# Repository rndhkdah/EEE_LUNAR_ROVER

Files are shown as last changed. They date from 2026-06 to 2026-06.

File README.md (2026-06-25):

# EEERover Specifications and Technical Guide
---

This GitHub project contains information on our electronics design project.

You will find
 - [Project Brief](doc/brief.md)
 - [Technical Hints](doc/README.md)
 - [A Marking Scheme](doc/deliverables-and-mark-scheme.md)
 - [Starter code for the Adafruit Metro M0 Express module](metro-starter-arduino/README.md)
   - [Starter code as a PlatformIO project](metro-starter-pio/README.md)
 - [Chassis design files](mech/)

---

## Project Management & Tasks

Quick links to our project planning and tracking documents.
You can fill in the task by yourself, cause I'm just copying the format you use on Notion. I do not know exactly what are the use of these.

- [Web UI Remote Control (Live Demo)](https://Albert14736.github.io/EEELunarRover2526-main/Sync%20files%20on%20GitHub/Tasks/SoftWare%20stuff/remote_ui_test.html) - Direct link to our deployed rover control interface (Phone/Desktop compatible).
- [Group 10 Master Doc (from Google Docs)](Sync%20files%20on%20GitHub/EEE%20Lunar%20Rover%20Group%2010.md) - **If you find it annoying to update multiple tracker files, just dump your progress, notes, or code snippets here** I will review this document regularly and organize/distribute the information into the proper folders for us.
- [Project Logbook / Diary](Sync%20files%20on%20GitHub/diary.md) - Our team's daily diary to record meetings and what we have achieved.
- [Team Workspace Guide](Sync%20files%20on%20GitHub/README.md) - [To be filled]
- [Demo](Sync%20files%20on%20GitHub/Projects/Demo.md) - [To be filled]
- [Interim Presentation](Sync%20files%20on%20GitHub/Projects/Interim%20Presentation.md) - [To be filled]
- [Report](Sync%20files%20on%20GitHub/Projects/Report.md) - [To be filled]
- [Parts Tracker](Sync%20files%20on%20GitHub/Tasks/Parts%20Tracker.md) - [To be filled]

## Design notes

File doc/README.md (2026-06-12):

# EEELunarRover Technical Guide

This guide has three main aims:
 - Document the additional hardware that you are provided with to get started
 - Specify the processes you will need to develop your design (e.g.~ordering components)
 - Provide some implementation ideas that you may find useful
	
 Most of the contents of this guide is advisory. You do not have to use your EEEBug or the items in the starter kit if you wish to pursue different ideas.
	
 ## Expansion Kit
 You are provided with some parts to use with your Lab-in-a-Box kit to get started:
 
| Qty | Description |
| --- | --- |
| 1 | Rock simulator  |
| 1 | Breadboard  |
| 2 | USB-A to Micro USB cable  |
| 2 | H-Bridge Motor Driver Module |	
| 2 | Adafruit Metro M0 Microcontroller Module |
| 2 | Adafruit WINC1500 WiFi Shield |
| 2† | Magnet |
			
You are given one expansion kit per group in your allocated shelf.
It is designed for use with your existing EEEBug chassis.
At the rear of the chassis is a mounting point for the Metro board and the central PCB has mounting points for the motor driver module.
The breadboard, as you have already seen, is ideal for prototyping circuits.
Finally, the design of the chassis is available to download that you can produce your own version.
    
### Motor Driver

The project kit contains a motor driver module to make it easy to control power to the motors.
The motor driver is an integrated *H Bridge* with decode logic, illustrated below.
The H-bridge allows current to be driven in either direction through the central load by connecting one terminal to the positive supply and the other to ground.

Circuit diagram of an H-bridge with logic decoder

The module contains two H-bridges, one for each motor.
Each channel has two digital inputs, DIR and PWM, which are decoded and used to control four MOSFETs.
The MOSFETs are driven with binary inputs so that they act as switches and the impedance is either very low or very high.
The motor driver module plugs into the motor power connectors on the EEEBug PCB.

The module inputs can be connected directly to digital outputs on the Metro board.
DIR controls the motor direction and the motor speed can be controlled by applying a rectangular waveform to the PWM input and varying the duty cycle — use `analogWrite()` in the Arduino API to generate a PWM signal.
			
### Metro M0 board

The Adafruit Metro M0 Express board is a embedded computing platform based on an ARM M0 microcontroller and compatible with the Arduino form factor, libraries and development tools.
It is programmed in C++ and features digital inputs and outputs, inputs with digital-to-analogue conversion and PWM outputs. Internet connectivity is provided by a Adafruit WINC1500 WiFi Shield, which plugs into the Metro board.

You are provided with demonstration code that shows the use of basic functions of the Metro board.
The WiFi interface is used to host a basic webpage, which you will see hard-coded into the demonstration code.
The webpage provides two links which, when pressed, turn on and off the onboard LED.
Use the Arduino Serial Monitor to connect to the board via USB and you will see some debug messages reporting on the connection status.
Whenever the webpage is retrieved you will see the HTML request made by the web browser.
			
Arduino is a popular platform for prototyping and you will find a lot of information and many code examples on the internet.
Use these resources but beware that many are provided by third parties and may not be well-written or even correct!
			
### Starter code

This repository contains [microcontroller code](../metro-starter-arduino/README.md) to get you started.
You can continue to use Arduino IDE as in the lab skills work, or you can develop with Visual Studio Code and Platformio.
			
 ### Connections and Power
 
> **Warning**
> 
> The logic level of the Metro board is 3.3V, which is supplied by an on-board voltage regulator.
> You will damage the board if you connect the input/output pins to a voltage greater than 3.3V.

Use potential dividers to reduce voltages greater than 3.3V and measure the output voltage of your circuits before connecting them to the inputs of the Metro board.
The safest option is to design add-on circuits with a 3.3V power supply.
Digital inputs should be 0V for logic low and 3.3V for logic high.
Analogue inputs should be in the range 0--3.3V.

Metro M0 Express Pinout
*Pinout for the Metro M0 Express module from [Adafruit](https://learn.adafruit.com/adafruit-metro-m0-express/pinouts)*

The pin locations and functions are broadly compatible with the Arduino layout used on the Orangepip Kona328 board used in the Microcontroller lab experiment.
The I/O pins pass through the WiFi Shield when it is connected, but the pins labelled CS, IRQ and RST on the WiFi Shield (Arduino pins 5,7 and 10) are used by WiFi and can't be used for other purposes. 

The Metro board can be powered by USB, the power jack or the EEEBug batteries.
To connect to the EEEBug batteries you will need to make the following connections between the Metro board and the EEEBug PCB:

- 5V → 5V
- GND → GND

> **Warning**
> 
> Always check connections before switching on the power.
> You may damage the microcontroller if you make a mistake
			
You can use the 5V or 3.3V nodes to power your own circuit.
It is not recommended to use Vin or Vbatt, since the voltage of these will vary depending on the power source.
The motors will run slowly if the battery is not available.
			
Simplified circuit diagram of the Metro M0 Express and EEERover PCB power supplies

*A simplified diagram showing the connection of the Metro M0 Express and EEERover PCB power supplies*
			
 ### Rock simulator
      
Your prototype will be developed and tested using rock simulators: electronic devices which can replicate the characteristics of the real rocks.
A rock simulator is included in your kit to aid development.
 
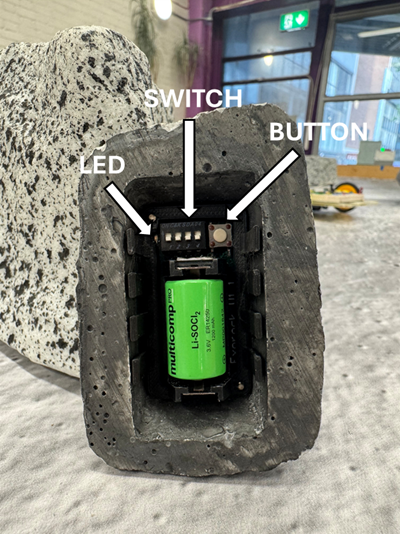
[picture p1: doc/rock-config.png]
User interface of the rock

					
The rock is configured by setting a group of DIP switches on its internal PCB. The switch, button, and LED are accessible without removing the PCB from the rock simulator.
A push button is used to turn it on and off, and an LED indicates when it is active.
A flow chart depicting the operation of the rock is shown below.
From standby (inactive) mode, press the button to turn on and observe the LED flashes to determine whether the battery has sufficient charge.
After the battery display sequence is complete the rock begins emitting signals according to the mode set up on the DIP switches.
The LED flashes a code at intervals to confirm the mode selection and indicate operation.

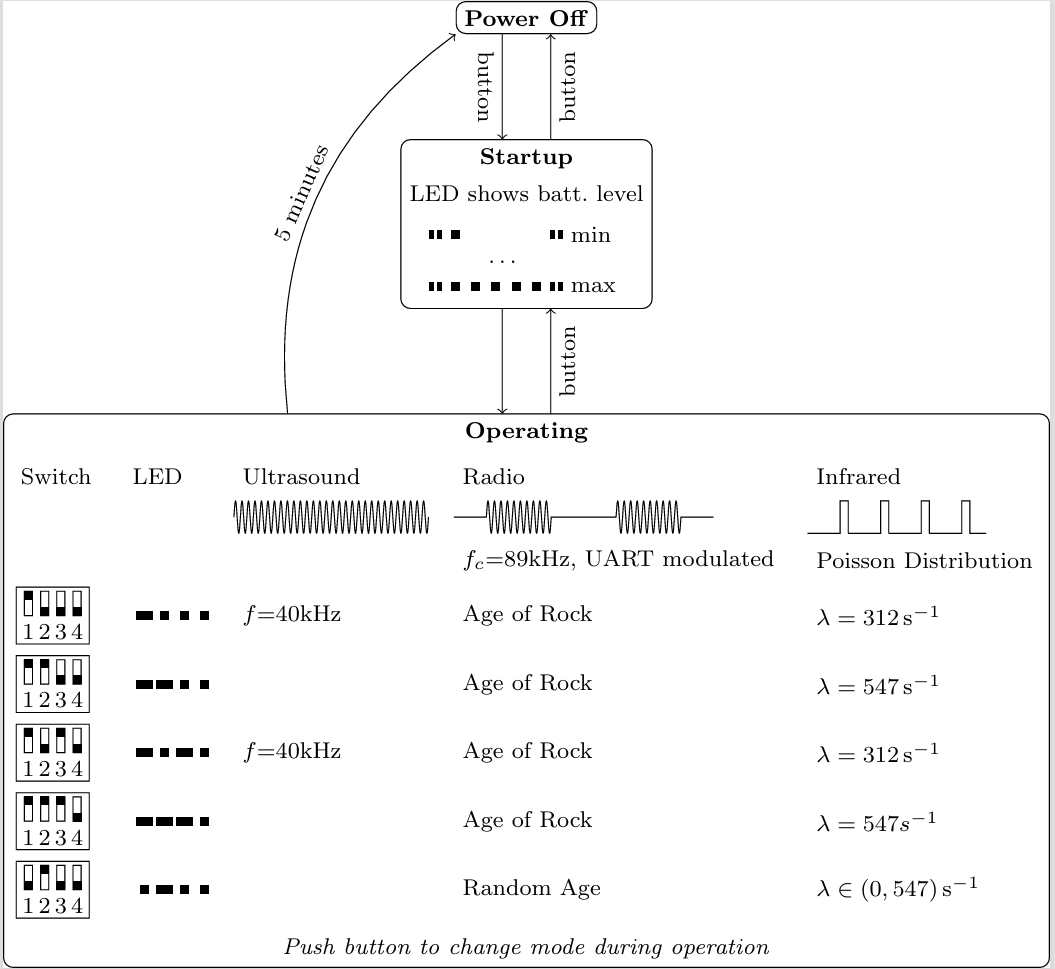
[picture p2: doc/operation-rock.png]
Operation flow chart for rock simulator


In normal operation, the rock communicate its age via radio — this will be the mode used in the final demonstration.
Other mode is available to help testing:
- The rock can communicate a random age and Poisson rate λ∈(0,547) s<sup>-1</sup>, which will change each time it is restarted.
		
Pushing the button during operation will reset the rock — this is necessary to change the operation mode.
A second press soon afterwards will turn the device off.
If the rock is left operating for five minutes it will automatically power off to preserve the battery.
			
The rock cannot simulate the magnetic property in an readily-configurable manner so you are provided with a small magnet to test this functionality.
In the demo, magnets will be placed inside a rock.
With the orange disc flat on a surface, the magnetic field is orientated down with the orange disc:

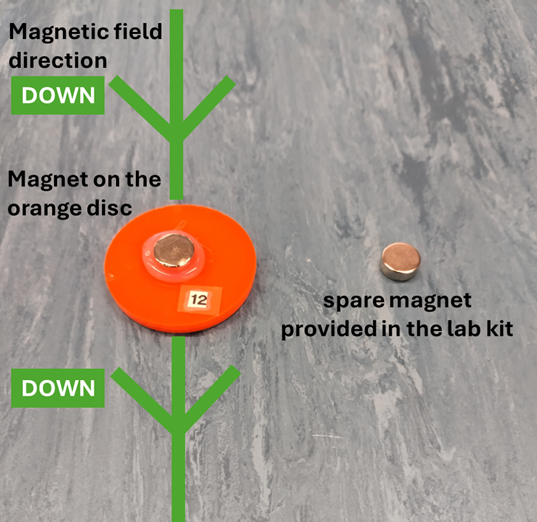
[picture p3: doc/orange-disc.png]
Magnetic field direction on an orange disk. With the disc flat on a surface, the magnetic field is orientated down with an orange disc


The radio signal is emmitted from a coil antenna in the plane of the PCB.	
			
 ## Components and Construction
 ### Ordering components

Each project group has a budget of £60 to cover all the additional components you'll need for designing and building your prototype. Each group must assign one member as the approver for their component orders. Orders will only proceed after approval from the approver of your group to prevent misordering or duplicate orders.

Your approver will order components by using Online Order Form in [EEE Stores Website](https://www.imperial.ac.uk/electrical-engineering/internal/stores/).

You will receive an email when the parts are available for collection from Stores on level 1, near the lifts. Orders, assuming the items are in stock, will take up to a week to arrive. You can order some components directly from stores stock and these will usually be available for collection sooner.
			
Please be aware of the following rules and common pitfalls when ordering components:
 - You must only order items that you can use safely. If you have any doubts about this then talk to a member of staff before ordering. Do not order batteries, chemicals (including glue), tools or mains-powered equipment/parts without consulting staff.
 - Always check that the supplier holds sufficient stock. If an item is out of stock it will be placed on back-order and it may take months to arrive. Try to find an alternative part or supplier instead.
 - Some suppliers offer stock from sister companies around the world. Do not order any items which warn about additional delivery charges.
 - Many electronic components are *surface mount*. This means that they sit on flat pads on a PCB instead of having flexible leads to insert into a prototyping board. They are also usually very small. You will find surface mount components difficult to use so avoid them by checking item descriptions and datasheets carefully.
 - You need to maintain the goodwill of the stores staff to order parts for this project and future projects. Do not chase the staff for your order until one week has passed from placing the order. It is your responsibility to order in good time and to check parts for suitability and availability.
			
### Making a new chassis
This repository contains design files for the EEEBug chassis.
You can design your own version using this as a template.
You will see that cut lines are drawn in red and engrave lines are drawn in blue.
Laser cutting removes a tapering width of material known as a *kerf*, which for 3mm acrylic is typically 0.1mm at the bottom of the material and 0.3--0.4mm at the top. Hence, cut edges are not vertical and external dimensions will be slightly smaller than drawn and internal dimensions slightly larger than drawn.

Designs for laser cutting must be submitted in PDF format.
Multiple parts can be placed on the drawing as long as they fit into an area of 600mm x 300mm.
Add engraving to identify your group as the owner.
You are strongly recommended to check your design by printing it on paper first — the scaling will be identical as long as the PDF file is printed at 100% scaling.

### 3D printing and Workshop facilities
A basic workshop is available in the lab.
Talk to Vic if you want to use it and be prepared to explain exactly what you want to do and demonstrate that you are capable of doing it safely.
You can also have components 3D printed if you are willing to learn the necessary design techniques independently.
Talk to Amine in the technicians' office if you would like to use 3D printing.
			
## Implementation Hints
The characteristics of rocks from the design brief are:
- Age (Radio)
- Types (Infrared, ultrasonic)
- Magnetism
			
### Age
  
The rock's age is encoded as ASCII characters and framed as UART packets in radio signal.

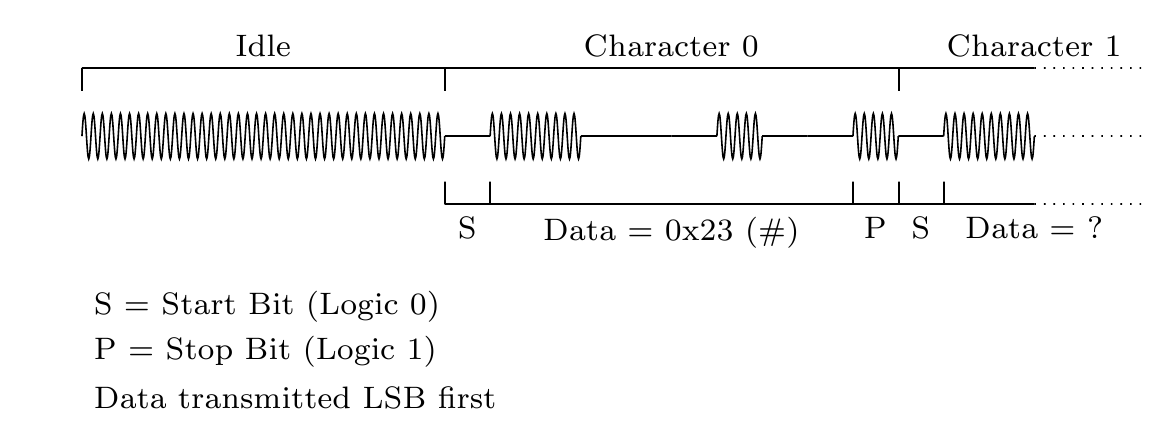
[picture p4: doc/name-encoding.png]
Name encoding


Radio communication uses a carrier frequency of 89kHz, modulated with a form of amplitude-shift-keying, where an amplitude of 0 represents logic 0 and an amplitude greater than 0 represents logic 1. 
First you will need to pick up the radio waves via an antenna. Then, you will need to convert the radio waves (ASK modulated radio signal, UART - given in the operation flow chart for rock simulator) into a signal.
You can use a tuned coil antenna, which is essentially an air-cored inductor with a reasonably large diameter that you can make by coiling wire.

This inductor can then be used in a tuned circuit that will be most sensitive at the resonant frequency.
The lab has *LCR Bridge* instruments that can tell you the inductance of your inductor.

The signal amplitude generated by your antenna will be small, so it will need amplification before you can extract the data.
The microcontroller will struggle to sample the radio signal at its carrier frequency so you will need to perform demodulation with *envelope detection* to produce a signal which indicates the amplitude of the signal.
The easiest way to do this is by rectification, but you may need a *precision rectifier* if your signal does not have enough amplitude to accommodate the voltage drop caused by a simple diode.
A precision amplifier needs an opamp with a relatively high slew rate. 

After demodulating the signal, you can convert the demodulated signal into a binary signal with a comparator, which compares the amplitude against a threshold.
A threshold can be set with a potential divider, or a more advanced approach is to derive it automatically from the average level of the signal with a low-pass filter.

As you saw in the Lab Skills work, microcontrollers have UART communication built in, and you can use your Metro module to automatically decode the demodulated binary signal into bytes.
In the Orangepip, communication to the host PC used the same UART port as the signals presented on pins 0 and 1.
However, the Metro board has two independent UART ports so you can use one to send debugging information over USB and a different port on pin 0 to receive messages from the rock.
The two ports can operate at different bit rates.
			
### Types
The types of a rock is indicated by an infrared signal pulse rate with a Poisson distribution, ultrasonic signal and magnetic fields.
For infrared signal, you have already made a light sensor as part of the EEEBug and most silicon-based photosensors (such as the EEEBug phototransistor) are just as sensitive to infrared as visible light.
You will need to measure the infrared pulses rate and this can be done with analogue or digital methods.

The optical power given by the rock is weaker than the light source you used for the EEEBug so you may need to amplify the output.
Ambient light will cause interference and this can be filtered out by using a sensor that is only sensitive to the wavelength of the rock emission (950nm) and by using electronic filters.
Many sources of electric light have a strong frequency component at 100Hz due to the rectification effect of the 50Hz AC source.

The infrared pulse rate is approximately λ=547 s<sup>-1</sup> or λ=312 s<sup>-1</sup> depending on the type of a rock. The pulse width of the infrared signal is just 50μs and the amplitude that you observe will be reduced if you filter out the high frequency harmonics. Low-pass filtering may smooth out the edges of the pulse and make pulse rate measurement less accurate. There can even be a problem with the sensor itself, since all optical sensors have a capacitance that acts to introduce a low-pass filter. There may be a trade-off between the speed and the sensitivity of your sensor.

A recommended method for measuring random infrared pulse rates on a lab oscilloscope is described below.

1. View pulses on the oscilloscope with a 10ms timebase.
2. Add measurement for 'Count' (positive or negative pulse depending on signal).
3. Use the 'single' button to capture and count one screen of the signal. The oscilloscope shows 12 divisions at 10ms, so the measurement is the pulses counted in 120ms.
4. You can confirm that the count measurement matches the number of pulses visible on the screen, but you should use the 'Zoom' view to be able to distinguish closely spaced pulses.
5. Use the single button to make as many measurements as necessary to get a statistically significant result.

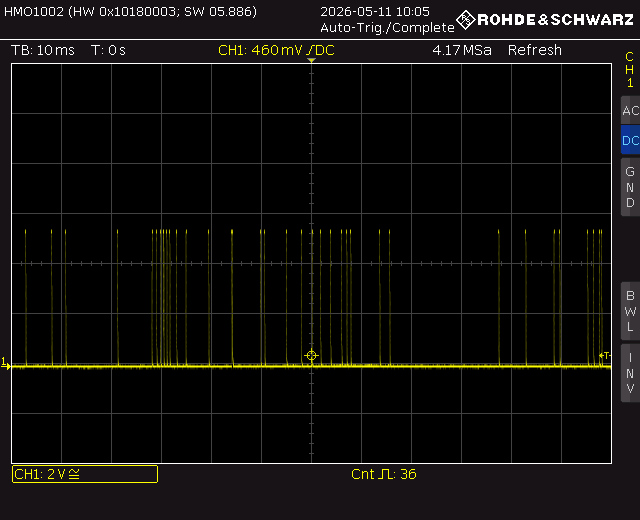
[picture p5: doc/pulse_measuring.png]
Measuring the infrared pulses rate on the oscilloscope


For the ultrasonic system, you will need to pick up the ultrasonic signal by placing a suitable ultrasonic transducer near a rock. Then, the classification of the rock can be done based on the ultrasonic signal presence (40kHz) or absence.
			
### Magnetism
The magnetic field of the rock is static, meaning that it will not induce a current in a coil of wire unless that coil is moving.
A moving coil is a possibility, but there are also sensors and switches that can detect a static magnetic field.
Test any new components and read their datasheets to determine if any amplification or signal processing is required.
Many sensors are designed to detect if a mechanism is open or closed (e.g. a laptop screen), and they may not work well in this application because the magnetic field may be weak due to the distance of the sensor from the magnet.
Furthermore, you need to determine the direction of the magnetic field, whether it is up or down. In the demonstration, magnets will be placed inside a rock as shown below.

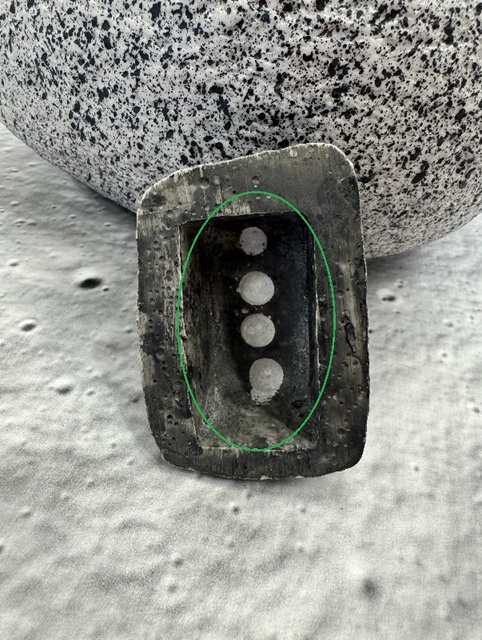
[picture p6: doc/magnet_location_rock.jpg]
Magnet location in rock

   
### Opamps
You may wish to implement amplification or filtering using an opamp.
There are many different opamps and they have different specifications.
Some manufacturers have parametric search facilities on their websites to narrow down the options based on your specifications. Use the opamp knowledge you obtained last term and conduct your research to choose suitable opamps for your applications.

There are some important parameters to consider:
- The opamp must operate at the available power supply voltage. Some opamps are design for use at higher voltage.
- You may need an opamp that offers *rail-to-rail* input and output, which allows you to make full use of the supply voltage.
- If the opamp output needs to switch quickly then the *slew rate* will be important. This will be a consideration in comparator and rectifier circuits. The LT1366 has a low slew rate.
- For high-gain circuits, check that the *gain-bandwidth product* is sufficient at the signal frequency you are using.

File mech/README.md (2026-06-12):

 # Chassis Design Files
 
 These files contain the design for the original EEEBug chassis. You can use them to design a modified chassis for your EEERover. There are three formats:
 
 - .dxf - This is a technical drawing format for CAD software
 - .svg - This is a drawing format that you can edit with vector graphics software like Inkscape. The width of lines must be set to 0.01mm for the laser cutter to interpret them as linear cuts.
 - .pdf - Your production file for the technicians should be in pdf format. Print it on paper at 100% scale to make sure the dimensions are correct. Red lines (#FF0000) are a complete cut and blue lines (#0000FF) are for engraving.

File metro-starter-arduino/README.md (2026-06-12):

# EEERover starter code

This project is an example of setting up WiFi communication with the Metro M0 Express module using HTTP.
The microcontroller connects to a WiFi network and acts as a simple web server, returning a basic web page when it receives an HTTP request.
It also acts on certain paths in the HTTP request to switch an LED on and off when the client clicks buttons on the webpage.

## Building the project

Additional libraries are needed to use Arduino IDE with the Metro M0 board and WiFi module. [Follow the instructions from Adafruit](https://learn.adafruit.com/adafruit-metro-m0-express/arduino-ide-setup) to add support for the Metro M0 Express board in Arduino IDE. Alternatively, you can build the project in [Visual Studio Code using PlatformIO](../metro-starter-pio/README.md).
			
The WiFi communication functions are provided by the WiFiWebServer library, which also must be installed with the Library Manager. The library installs its own set of example sketches and has an [API reference](https://github.com/khoih-prog/WiFiWebServer). The demonstration code in this repository is based on these examples.

## Network configuration

The code is configured to connect to the EEERover network in the lab. You can give a different WiFi network and password, such as a mobile hotspot, by changing the appropriate lines in the code. You won't be able to connect to the College WiFi network, which uses a login. When the code starts it reports its IP Address on the serial monitor. You can connect to the microcontroller from a computer on the same WiFi network by typing this address into a web browser. WiFi functions are provided by the [WiFi101](https://www.arduino.cc/reference/en/libraries/wifi101/) library.

You may need to connect to the microcontroller when it is not connected with a USB cable, so you won't see the message reporting the IP address. You can fix the IP address to a certain value by setting `groupNumber` to your group number. The IP address will be `192.168.0.n+1`. You can only do this on the EEERover network because it has been configured to allow a certain range of static IPs.

## HTTP server

The [WiFiWebServer](https://github.com/khoih-prog/WiFiWebServer) library is used to handle HTTP requests from WiFi clients.
HTTP is the protocol used to access websites and it is used here because it allows the creation of a simple user interface using a web browser.

The server is configured in the `setup()` function using calls to `server.on()` to define what happens when requests are received.
Each HTTP request has a URI, which is the path of the resource that is requested. The server responds to three different URIs:
 - `/` The root path, e.g. `http://192.168.0.10/`
 - `/on` A request to turn the LED on, e.g. `http://192.168.0.10/on`
 - `/off` A request to turn the LED off, e.g. `http://192.168.0.10/off`

A different function is called when each request is received. A request to the root path returns the html code for the user interface. `/on` and `/off` set the LED and the reponse is the state of the LED, either `ON` or `OFF`.

### The web interface

The webpage built into the starter code is a basic user interface based on JavaScript and HTTP requests. `<button>` tags are used to define two buttons, which are formatted with some basic styling defined in the `<style>` section. Each button triggers a JavaScript function that is defined in the `<script>` section. In these functions, a [XMLHttpRequest](https://developer.mozilla.org/en-US/docs/Web/API/XMLHttpRequest/Using_XMLHttpRequest) object is used to send a HTTP request with its `send()` and `open()` methods. 

An inline function is assigned to `xhttp.onreadystatechange`, which is called whenever a response is received to a HTTP request. The function updates the LED state text displayed on the page with the contents of the HTTP response. Remember that all the JavaScript functions are executed on the client web browser, not on the microcontroller module. You could host or store the webpage somewhere else entirely - you would just need to modify the URLs for the on and off HTTP requests to include the full hostname (IP address) of the microcontroller.

## Next steps

The code gives an example of sending information in both directions between the microcontroller and the remote client.
It can be extended to include all the data you need to control your rover and get data back.

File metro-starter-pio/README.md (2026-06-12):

# EEERover starter code for Platformio

Download Microsoft Visual Studio Code and install the Platformio extension. Open Platformio Home using the link in the Platformio sidebar or the 🏠 (home) icon on the bottom toolbar. Choose 'Open Project' and select the directory containg this README.

Build the project using the Build option in the Platformio sidebar or the ✓ icon on the bottom toolbar. Platformio will download the required libraries and board support package the first time you build the project.

Run the code by choosing 'Upload' or →. View the serial output using 'monitor' or 🔌. A terminal will open to show the serial output from the microcontroller.

Refer to the documentation for the [Arduino IDE version](/metro-starter-arduino/README.md) of the starter code for more information.

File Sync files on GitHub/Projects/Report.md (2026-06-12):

# Final Report & Reflection

**Date of Submission:** 11 June 2026
**Weighting:** 40%

## Deliverables
1. **Main Group Report**: Formal documentation of all technical and non-technical work. Justify all design decisions and include test results.
2. **Professional Reflection Forms**: Must be prepared individually and added to the appendix (Must pass component!).

## Proposed Report Structure
- **Introduction**: Project brief and objectives.
- **Hardware Design**: Circuit diagrams, op-amp calculations, sensor selection (e.g., SS49E hall sensor).
- **Software Design**: State machine, WiFi communication, UART decoding, filtering algorithms.
- **Testing & Results**: Oscilloscope screenshots, motor diagnostic logs (e.g., test on 13/05).
- **Project Management**: Budget tracking, task allocation, timeline.
- **Conclusion & Future Improvements**.

*Note: One team member should act as the overall editor to ensure consistency in style and content.*

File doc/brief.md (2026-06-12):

# ELEC40006 Electronics Design Project 
## Project Brief: EEELunarRover
	
## Introduction
	
The Electronics Design Project is one of the six modules that make up your first year of study.
It brings together theoretical and practical content from your lectures and labs with important industrial skills relating to product design, project management and team working.
		
You will work in tutorial groups of 6 people to complete the project.
It will be assessed with an interim interview, a final report that includes a professional reflection forms (must pass component), and a demo.
		
## Brief

You are requested to design a remotely-controlled lunar rover, EEELunarRover, that can survey the lunar surface and classify the rocks there.
Using a variety of electromagnetic signals, you must find out the age and types of each rock.

Artificial Lunar Surface
  
A prototype of the design must be built and tested in an artificial environment in the lab.
The quality of the design will be assessed against the following criteria:
- Is it possible to find the characteristics of all the rocks?
- Is the design cost and weight effective?
- Is the rover manoeuvrable enough to negotiate the environment?
- Is the construction robust and reliable?
- Is the remote control interface logical and easy to use?
	
## Characteristics of the rocks
### Age

The rocks transmits data via a radio using 89kHz carrier frequency, which is modulated with two-level *amplitude-shift keying* (on off modulation).
The age is encoded using ASCII character codes in UART packets with 1 start bit and 1 stop bit.
The data rate is 600 bits per second and each rock's age is four characters long, including an initial `#` symbol. If you receive `#123`, it will mean the rock's age is 1.23 billion. 
	
Rock age encoded in radio frequency
	
### Types

The rocks look same, but their colour and shape are superficial. You will need to examine other characteristics - infrared, ultrasonic and magnetic - to determine the types of a rock. The rocks emit radiation events randomly in time with a Poisson distribution which can be measured using an infrared detector on your rover. Infrared pulse rate will give information about the radioactivity levels of the rocks. Your rover will count the radiation event (infrared pulse rate) in the rocks to classify their radiactivity and type. Basaltoid and Lunarite are more radioactive than Gravion and Regolix. 

The characterisitics of each types are defined below:

| Types  | Infrared | Ultrasound | Magnetic |
| --- | --- | ----- | --- |
| Basaltoid  |λ=547 s<sup>-1</sup> | 40kHz | Down |
| Gravion  |  λ=312 s<sup>-1</sup> | | Down |
| Regolix | λ=312 s<sup>-1</sup>  | 40kHz | Up |
| Lunarite | λ=547 s<sup>-1</sup> |  | Up |

> [!NOTE]
> Please expect small deviations in the given values for Infrared pulse rate.

## Deliverables and assessments
	
The project will be assessed with an interim interview, a final report that includes a professional reflection forms (must pass component), and a demo with and interview and head-to-head competition.

### Interim Presentation

**Date of assessment:  28 May 2026**

The interim presentation is an opportunity to show your progress mid-way through the project.
You should prepare a presentation showing your high-level design, research and technical progress so far.
You should also present a plan for the remaining work to complete the project.

Marks weighting: 20%
	
### Report

**Date of submission:  11 June 2026**

The report is a formal documentation of all the technical and non-technical work you have done on the project.
The report should justify all your design decisions and include test results of various aspects of your prototype.
One team member should act as overall editor to ensure that the report is consistent in style and content.

Marks weighting: 40%

### Professional Reflection Form

**Date of assessment:  11 June 2026**

Professional Reflection Forms will be prepared individualy and added to your group project report appendix.

Marks weighting: 0% (must pass component)

### Demo

**Date of assessment:  16 June 2026**

The demo is your opportunity to present your completed project.
There are two parts to the demo:
1. An assessment of your rover on the lab bench, where your examiner will ask to see different functional aspects and assess your theoretical understanding of the implementation
2. A test of your rover on the demonstration arena, where multiple groups will compete to classify all the rocks in the quickest time.

Marks weighting: 40%
	
## Getting started
				
### EEEBug Expansion Kit
Your EEEBug has been designed to support modification for work on this project.
The Orangepip will be replaced with an ARM-based microcontroller platform with a WiFi module, but you can continue to develop code using the Arduino framework and IDE.
The central PCB has connections for a motor driver module, which will simplify the challenge of steering and reversing your rover.
			
### Sensing
You should use the outcome of your lab experiments to develop ideas for making sensors and analogue interfaces to detect the signals.
The EEEBug experiment showed you an example of an optical sensor.
The Passive Networks experiment (Autumn Term) introduces the concept of resonant circuits which, if the inductor is suitably constructed and orientated, will oscillate in the presence of radio waves of the correct frequency.
Magnetic sensors are not covered directly in the labs and you should carry out your own research in this area. Likewise ultrasonic transducers, which are usually designed to resonate at a specific frequency.
			
In certain cases you may wish to detect particular frequencies while blocking others, and you have explored to do this with passive and opamp-based circuits.
Some sensors will produce a weak signal that will need amplification.

Signals will need to be converted into the digital domain for transmission back to the rover operator.
Consider whether a binary input is sufficient, or you need to measure the voltage with more precision.
Research software libraries that can help you determine time-domain characteristics such as frequency or serial data encoding.
			
### Construction
Mechanical design is not a core component of the EEE/EIE degree so it is left to you to be innovative in the construction of your rover.
The EEEBug chassis is designed to be a useful platform but feel free to modify it, taking into account the budget and weight constraints.
			
You can download a computer-aided manufacturing (CAM) drawing of the chassis, which can be modified for reproduction in acrylic with a laser cutter.
Workshop facilities are available on arrangement with the lab technicians.
You may wish to consider 3D printing, though you will need to research and teach yourself the necessary techniques first.
3D printers are available to use with the help of the lab technicians.	

### Demo Environment
The demo environment has a grey coloured rubber flooring with some uncrossable obstacles.
Rocks will be distributed across the environment on the demo arena floor, spaced at least 500mm apart.
The arena is fitted with sensors in one area to check the weight of your rover. If your rover is heavier than 750grams, then it will fail classifying the rock in the weight sensitive zone on the lunar surface due to extremely loose and fragile surface there.

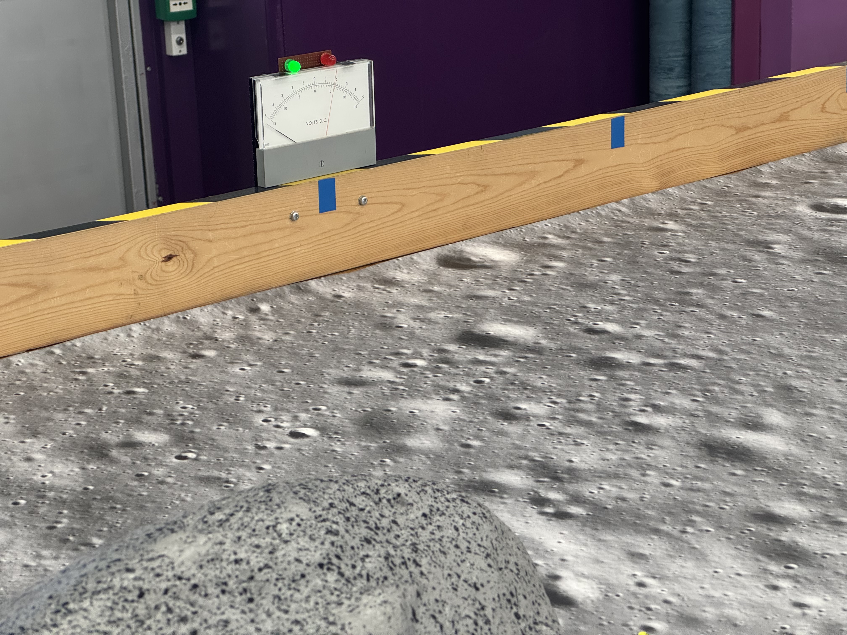
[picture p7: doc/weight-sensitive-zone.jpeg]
Weight Sensitive Zone


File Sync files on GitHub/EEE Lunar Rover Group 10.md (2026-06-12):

**<u>EEE LUNAR ROVER GROUP 10</u>**

<table>
<thead>
<tr>
<th>Group Members</th>
<th>Role</th>
</tr>
<tr>
<th>Mohammed Salem</th>
<th rowspan="2">Movement + User interface</th>
</tr>
<tr>
<th>Albert Ma</th>
</tr>
<tr>
<th>Devesh Kemani</th>
<th>Magnetism Detection</th>
</tr>
<tr>
<th>Christopher Koh</th>
<th>Project Manager + Infrared Detection</th>
</tr>
<tr>
<th>Wangmo Koo</th>
<th>Ultrasonic Detection + Parts IC</th>
</tr>
<tr>
<th>Ye Zifan</th>
<th>Age Detection</th>
</tr>
</thead>
<tbody>
</tbody>
</table>

**<u>TIMELINE</u>**

28 May - Interim Presentation

11 June - Report + Reflection Form

16 June - Demo

Components to order

| Item | Cost (pounds) | Min quantity |
|---|---|---|
| SS49E hall sensor | \<1 | |
| | | |
| | | |
| | | |
| | | |
| | | |

Steering

Receiving signals:

- Radio (age)

- Infrared

- Ultrasonic

- Magnetic

Weight (max 750g)

HARDWARE

[<u>https://www.keysight.com/used/gb/en/knowledge/guides/voltage-regulators</u>](https://www.keysight.com/used/gb/en/knowledge/guides/voltage-regulators)

**Report writing tips**

- See teams document

- Ensure narrative flow of report

- 

**INTERIM PRESENTATION**

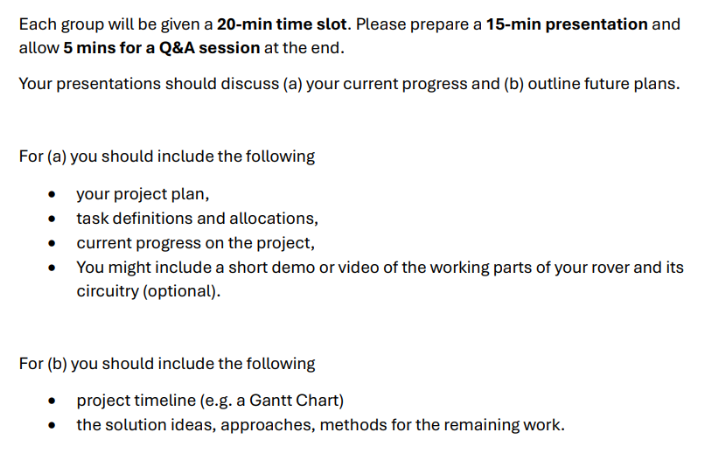
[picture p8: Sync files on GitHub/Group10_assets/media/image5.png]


**MAGNETISM DETECTION (DEVESH)**

<u>Sensing magnetic fields</u>

Hardware: SS49E hall sensor

Pin 1 (VCC): Connect to 3.3V on your Metro board.

Pin 2 (GND): Connect to GND.

Pin 3 (Output): Connect to an analog pin, like A0.

Metro M0 converts the voltage into a number 0-1023 using the analogue to digital converter

When no magneti near by - supply voltage = 1.65ishV and analogRead() will return a value near 512.

As a North pole approaches, the voltage rises toward 3.3V value moves toward 1023

As south pole approaches, the voltage drops toward 0V (value moves toward 0).

Magnetic field strength is proportional to r^3 so might only detect small changes. If the signal is too weak use Opamp as a non-onverting amplifier. MCP6002 opamp and build on breadboard

**Get op amp working, in slides talk about challenges that voltage signal isnt strong enough and solution w op amp. Do research into how magnetic sensor works and background knowledge for Q and A. run basic code from laptop. Write future part (talk about mount).**

**2-4 inclusive slides are my part**

Measure is +vs or-ve depending on which face of the sensor the magnet goes on, if magnet south puth faces magnet at all times.

0-1.8 in reality (in specs its0.2-1.8)

since 1V is when there is no sensor, the digital reading is 310.

Op amp

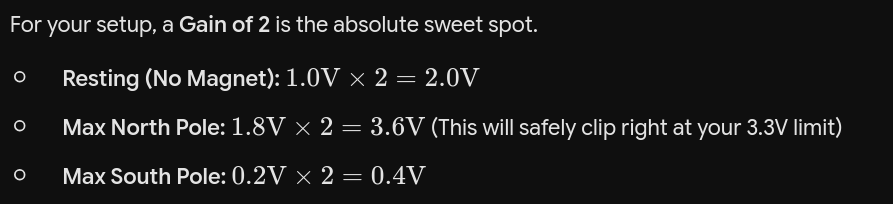
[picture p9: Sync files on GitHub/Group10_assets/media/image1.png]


Need to be literally touching the magnetic for 1.8v reding anyways so gain of 2 works as we will knoe if its in our face regardless that 0.3 v range we lose is negligible



Sample code:

void setup() {

Serial.begin(9600);

}

void loop() {

int sensorValue = analogRead(A0);

// 512 is the middle. We add a buffer of +/- 50 to avoid noise.

if (sensorValue \> 560) {

Serial.println("Magnetic Field: UP (North)");

} else if (sensorValue \< 460) {

Serial.println("Magnetic Field: DOWN (South)");

} else {

Serial.println("No strong magnetic field detected.");

}

delay(200);

}

- The motors or whatever else may create a magnetic field o their own so in the setup we need to account for that and records that value - 0 it out.

- Need to also account for rolling average, eg if value rises from 510 to 512 it doesnt necessarily mean we are moving closer to a rock. Therefore we should use a rolling average (eg the value of the reading is the average of the last 4 ‘snapshots’). Can achieve this simply with an array

- Need to account for other rocks magnetism in the code but i dont know how strong the other rocks magnetism will be

- 

Positioning:

- Point face (side with writing) down and point forward (closest to rock)

- Positing furthest away from motors

- 3D print a mount that can connect to the pins

const int hallPin = A0;

// Rolling Average Configuration

const int numReadings = 8; // Size of the filter window. Higher = smoother but slightly slower response.

int readings\[numReadings\]; // Array to store the raw ADC snapshots

int readIndex = 0; // Current position in the array

long total = 0; // Running sum of the array

int average = 0; // The smoothed output

// Baseline Configuration

int baselineValue = 0; // This will store the "zeroed out" resting value

void setup() {

Serial.begin(9600);

// --- 1. ZEROING OUT THE MOTORS (CALIBRATION) ---

Serial.println("Calibrating baseline...");

Serial.println("Ensure motors are running at default idle and magnets are far away.");

delay(2000); // Give the motors 2 seconds to spin up and stabilize their magnetic field

long calibrationTotal = 0;

int calibrationSamples = 50; // Take a deep average to find the absolute center

for (int i = 0; i \< calibrationSamples; i++) {

calibrationTotal += analogRead(hallPin);

delay(10);

}

// Set the new dynamic "middle" (Should be roughly around 310)

baselineValue = calibrationTotal / calibrationSamples;

Serial.print("Calibration complete. Baseline set to: ");

Serial.println(baselineValue);

// --- 2. PRE-FILL THE ROLLING AVERAGE ARRAY ---

// We fill the array with the baseline so the math doesn't start at 0 and falsely trigger

for (int i = 0; i \< numReadings; i++) {

readings\[i\] = baselineValue;

total += baselineValue;

}

}

void loop() {

// --- 3. ROLLING AVERAGE FILTER ---

// Subtract the oldest reading from the total

total = total - readings\[readIndex\];

// Read the newest raw value from the sensor

readings\[readIndex\] = analogRead(hallPin);

// Add the newest reading to the total

total = total + readings\[readIndex\];

// Advance to the next position in the array

readIndex = readIndex + 1;

// Wrap around to the beginning if we hit the end of the array

if (readIndex \>= numReadings) {

readIndex = 0;

}

// Calculate the smoothed average

average = total / numReadings;

// --- 4. MAGNETIC FIELD DETECTION ---

// Calculate how far we've deviated from the zeroed-out motor baseline

int deviation = average - baselineValue;

// Using a threshold of +/- 30 to avoid any remaining noise slipping through

if (deviation \> 30) {

Serial.print("North Pole Approaching! Signal Strength: ");

Serial.println(deviation);

} else if (deviation \< -30) {

Serial.print("South Pole Approaching! Signal Strength: ");

Serial.println(abs(deviation));

} else {

// If the deviation is between -30 and 30, we consider it clear

Serial.println("Clear. No strong magnetic rocks nearby.");

}

// A small delay for overall stability

delay(50);

}

**MOVEMENT (ALB**

**ERT)**

<u>How the robot can be controlled</u>

We should manually control the robot so that it can move towards the rock and gather sensor readings.

We can’t use the pins 5, 7, 10 since they are used by the WifiShield.

\[Reference to README file :

<span class="mark">The I/O pins pass through the WiFi Shield when it is connected, but the pins labelled CS, IRQ and RST on the WiFi Shield (Arduino pins 5,7 and 10) are used by WiFi and can't be used for other purposes.</span> \]

Therefore we should use other pins to control the motor.

THerefore we should use:

- Right : EN(8), DIR(9)

- Left : EN(11), DIR(12)

ENABLE wires are coloured orange

DIRECTION wires are coloured blue.

<u>13/05</u>

Connected PCB to Metro board and uploaded the code motor_move_v1 to test if the motors are connected properly.

\`\`\`v1

const int DIR_LEFT = 12, EN_LEFT = 11, DIR_RIGHT = 9, EN_RIGHT = 8;

void setup() {

Serial.begin(9600);

pinMode(DIR_LEFT, OUTPUT); pinMode(EN_LEFT, OUTPUT);

pinMode(DIR_RIGHT, OUTPUT); pinMode(EN_RIGHT, OUTPUT);

digitalWrite(DIR_LEFT, LOW); digitalWrite(EN_LEFT, LOW);

digitalWrite(DIR_RIGHT, LOW); digitalWrite(EN_RIGHT, LOW);

}

void loop() {}

\`\`\`

Test failed motors did not move, DC voltage 6.21 around battery terminal and 0.125A measured current through battery.

I found a wire that had not been placed properly (5V wire connecting board and PCB) fixed the issue and ran the code again.

Rewrote the code as well.

RESULT : LEFT motor was working fine but the right motor was not operating

The issue is that the motor on the right side works, however the pin12 is contested with the signal from the wifi module therefore we will use other pins to deliver the data. Suggested pins : DIR_LEFT = 2, EN_LEFT = 3

Rewritten code:\
const int DIR_LEFT = 12;

const int EN_LEFT = 11;

const int DIR_RIGHT = 9;

const int EN_RIGHT = 8;

// Speed for tests (0-255). 200 is a good starting point - high enough

// to overcome stiction, low enough to be safe on the bench.

const int TEST_SPEED = 200;

void setMotor(int dirPin, int enPin, int speed) {

// speed: -255 to +255. Positive = forward, negative = reverse, 0 = stop.

if (speed \>= 0) {

digitalWrite(dirPin, HIGH);

analogWrite(enPin, speed);

} else {

digitalWrite(dirPin, LOW);

analogWrite(enPin, -speed);

}

}

void stopBoth() {

setMotor(DIR_LEFT, EN_LEFT, 0);

setMotor(DIR_RIGHT, EN_RIGHT, 0);

}

void setup() {

Serial.begin(9600);

while (!Serial && millis() \< 3000) { ; } // wait briefly for serial monitor

pinMode(DIR_LEFT, OUTPUT);

pinMode(EN_LEFT, OUTPUT);

pinMode(DIR_RIGHT, OUTPUT);

pinMode(EN_RIGHT, OUTPUT);

stopBoth();

Serial.println("Motor diagnostic - no WiFi");

Serial.println("Watch each motor in turn.");

delay(1000);

}

void loop() {

// --- Right motor alone ---

Serial.println("RIGHT motor: forward");

setMotor(DIR_RIGHT, EN_RIGHT, TEST_SPEED);

delay(2000);

Serial.println("RIGHT motor: stop");

setMotor(DIR_RIGHT, EN_RIGHT, 0);

delay(1000);

Serial.println("RIGHT motor: reverse");

setMotor(DIR_RIGHT, EN_RIGHT, -TEST_SPEED);

delay(2000);

Serial.println("RIGHT motor: stop");

setMotor(DIR_RIGHT, EN_RIGHT, 0);

delay(1500);

// --- Left motor alone ---

Serial.println("LEFT motor: forward");

setMotor(DIR_LEFT, EN_LEFT, TEST_SPEED);

delay(2000);

Serial.println("LEFT motor: stop");

setMotor(DIR_LEFT, EN_LEFT, 0);

delay(1000);

Serial.println("LEFT motor: reverse");

setMotor(DIR_LEFT, EN_LEFT, -TEST_SPEED);

delay(2000);

Serial.println("LEFT motor: stop");

setMotor(DIR_LEFT, EN_LEFT, 0);

delay(1500);

// --- Both motors together ---

Serial.println("BOTH motors: forward");

setMotor(DIR_LEFT, EN_LEFT, TEST_SPEED);

setMotor(DIR_RIGHT, EN_RIGHT, TEST_SPEED);

delay(2000);

Serial.println("BOTH motors: stop");

stopBoth();

delay(2000);

}

The robot has its ends connected in the other way around.

We can fix this by the software or just connecting the wires to different parts around.

**AGE DETECTION (MOHAMMED + ZIFAN)**

**ULTRASONIC DETECTION (HARRY)**

**<u>Background</u>**

The rover will need to differentiate rocks based on the presence of multiple signals. The ultrasonic circuit will determine whether a 40kHz ultrasonic signal is emitted, after the presence of an infrared signal is found, it will be able to classify the type of rock.

Below is the table of types of rock and its corresponding signal presence

| **Types** | **Ultrasound signal presence** | **IR Rate** |
|---|---|---|
| Basaltoid | True | 547s^-1 |
| Gravion | False | 312s^-1 |
| Regolix | True | 547s^-1 |
| Lunarite  | False | 312s^-1 |

Ultrasonic presence separates {Basaltoid and Regolix } from the rock types, then the infrared rate will be used to distinguish within each pair (NO ultrasonic or when it exists). The role of this circuit would be to generate a clean logic signal representing the presence of an ultrasonic signal.

**<u>Design Process</u>**

**<u>Requirements</u>**

The circuit should follow these points;

- Detects the presence or absence of a 40kHz acoustic signal.

- Reject signal out of domain, which could be from motor vibration, ambient acoustic noise etc.

- Present the result to a microcontroller’s digital pin as a clean digital level.

- Able to detect presence of signal from a reasonable distance.

The raw signal from the 400SR-series receiver is a weak AC waveform and has a peak-to-peak value of roughly 10mV \[I need to measure the actual value in the lab\].

\[Picture of signal view on Oscilloscope, I can also use the auto-measure function\]

Therefore the signal should be amplified substantially before we can perform signal alteration operations.

**<u>Proposed Plan</u>**

Therefore we will be building a circuit with following stages to convert an AC signal received by the transducer and generate a clean DC logic signal.

Input : messy AC signal.

Output : Clean DC voltage output representing the presence of ultrasonic signal.

Transducer -\> Active Filter (Opamp with Band-pass-filters) -\> Envelope Detector -\> Comparator.

**<u>Expected change of signal</u>**

Expected change of signal would be as follows :

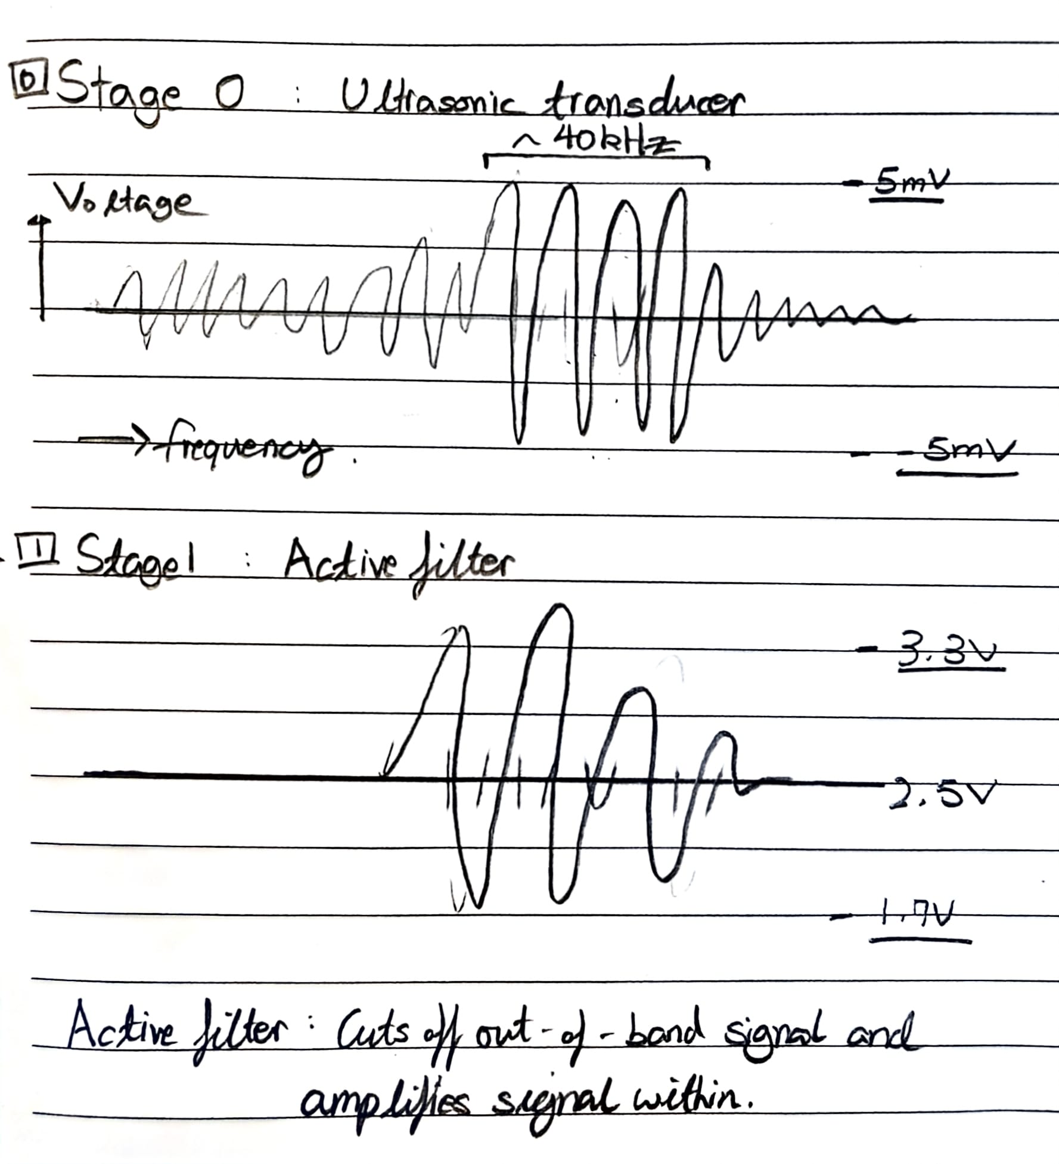
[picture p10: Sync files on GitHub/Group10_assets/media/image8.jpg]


> Unmodified signal from the transducer would be an AC signal with weak amplitude.

—-------------------------------------------------------------------------------------------



This part of circuit is an \`Active Filter\` This is used to filter out the parts that are out of band and amplify the signal within the specified range of frequency. We should also set up a

bias point around 2.5V to avoid

clipping the -ve part of the signal.

—---------------------------------------------------------------------------------------------

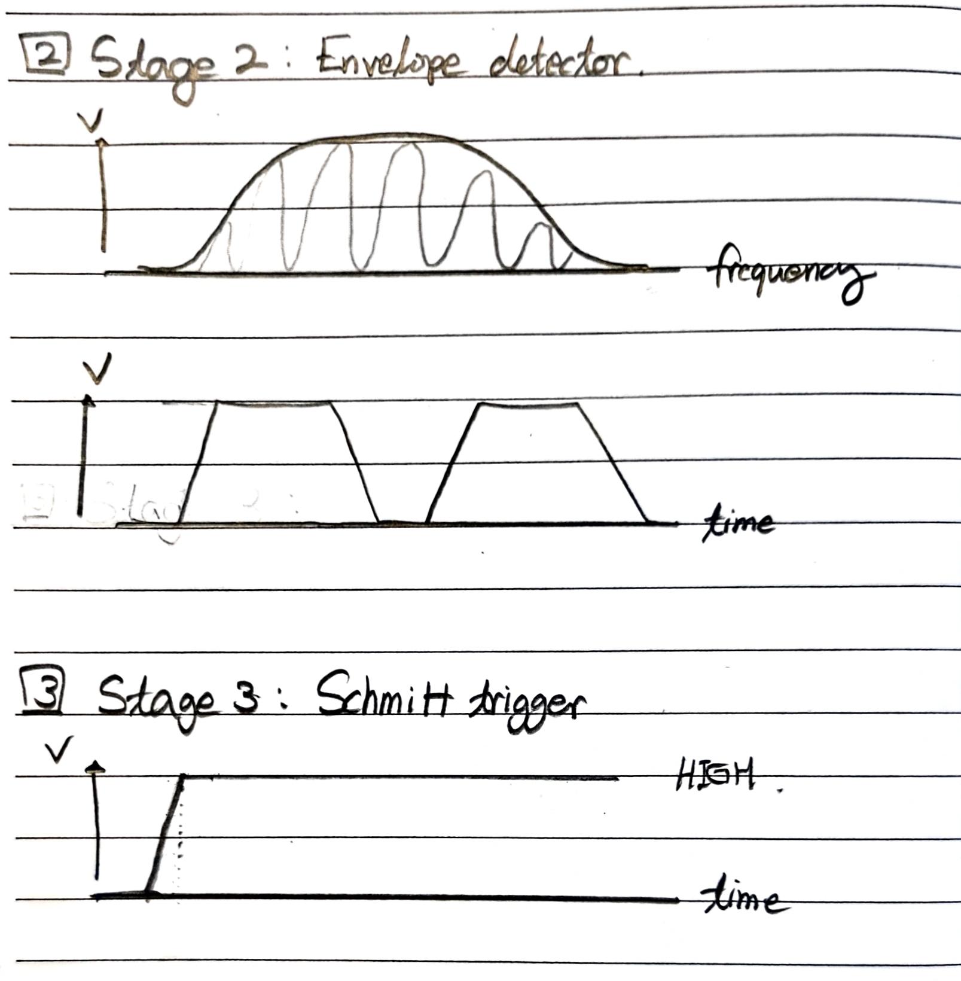
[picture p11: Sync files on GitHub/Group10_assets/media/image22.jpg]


Envelope Detector is used to smoothen out the alternating signal.

—---------------------------------------------------------------------------------------------

> Schmitt Trigger converts those pulses into a clean digital signal. With a high voltage outlining the presence and 0V representing the absence.

**<u>Component Selection</u>**

1.  Ultrasonic Transducer. (Used for stage 0)

Write about MCP6022, mention that its frequency is centered around 40kHz. Why would that be good?

Also explain that you chose this because of : (See Below)

h component and maybe some conditions or any notes to take.

Critical Evaluation :

We can discuss the \`Gain-Bandwidth product\`.

> For example, if the MCP6022 has a GBPWP of 10MHz, show that at the target frequency of 40kHz the maximum achievable gain per stage before phase shift or distortion is :
>
> 10Mhz (GBWP of MCP6022)
>
> Max Gain = ——---—------------------------------ = 250.

40kHz (Target frequency)

If I run out of things to write, I can write why I chose a rail-to-rail amplifier.

2.  Opamp

MCP6022,

We can talk about the following:

- 

3.  Diode (1N4148)

This diode has a 0.7V voltage gap.

4.  Comparator(LM393P)

> This is good because : \~\~\~\~~

Discuss what each component can provide.

## Technical Implementation

**<u>Circuit Architecture</u>**

- **Pre-Amplification Stage**

- **Amplification**

- **Envelope Detector**

- **Comparator**

### **<u>0. Pre-amplification Stage</u>**

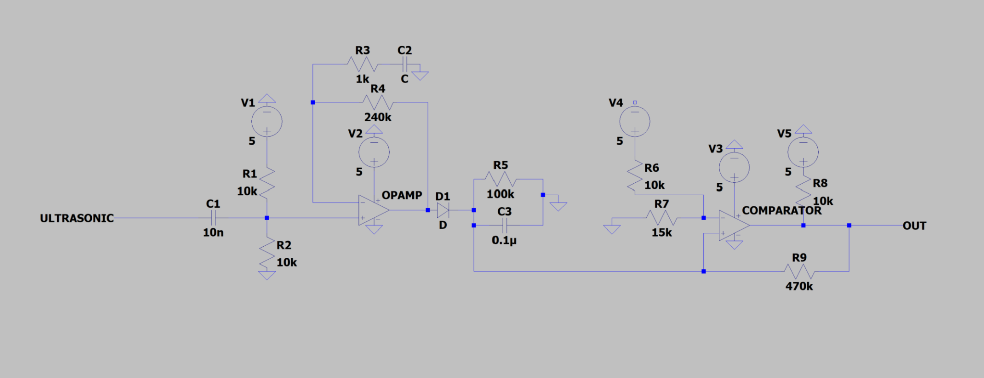
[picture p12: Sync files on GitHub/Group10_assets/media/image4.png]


An AC signal is received by the ultrasonic transducer (MCP6022), which oscillates at around (10mV). Feeding the raw AC signal into an op-amp would clip the negative half of the waveform, since the output cannot swing below the negative rail.

(Insert a picture of the Signal output from the raw transducer. Taking picture from Oscilloscope, also use auto measure to show that peak-to-peak value is around 10mV)

An AC signal is received by the ultrasonic transducer (MCP6022), which oscillates at around (10mV). Feeding the raw AC signal into an op-amp would clip the negative half of the waveform, since the output cannot swing below the negative rail.

Therefore I had set up a bias reference point using a potential divider circuit using R1 and R2 both set to 10k(ohms), at 2.5V, so that the signal now oscillates around 2.5V.

An input decoupling capacitor is placed in series with the transducer to block out any external DC offset while passing the AC signal.

#### Testing - Stage 1\

### **<u>1 - Amplifier with frequency filterings</u>**

The environment around the rover contains acoustic sounds and noises from motors, surroundings etc. In order to analyse the ultrasonic signal, we would have to isolate the signal around 40kHz to only get the ultrasonic signal.

1)  Passive High band pass filter (C1 and R2)

\[Components in charge : C1, R1, R2\]

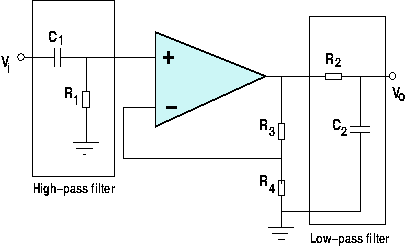
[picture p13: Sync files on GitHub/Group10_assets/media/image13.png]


> C1 not only acts as an AC input decoupling capacitor but also as a high band pass filter along with the resistor placed (R1 \|\| R2).
>
> This filters out the low-frequency noise before we apply gain to the signal through the opamp.
>
> Cut-off frequency is : 3.2kHz
>
> Calculation is ⇒

2)  Opamp - gain of 241.

\[Components in charge : OPAMP, R3, R4, C2\]

> We would like to amplify the signal by 241 (240 + 1 \[original\]), I chose this value because it will amplify the voltage above a level where it can be used by comparator and also for low-pass filter.

Gain is calculated by this equation : (1 + R4(feedback) / R3) = 1 + 240 = 241.

3)  Low-pass filter. (From the opamp GBWP)

> We would need to cut out the signal above the specified frequency (around 42kHz). This is done by the roll-off frequency determined by the transducer’s gain and its GBWP(Gain-Bandwidth-Product).
>
> Roll-off frequency = GBWP/Gain
>
> = 10MHz / 241

~= 42kHz

> Therefore the opamp also acts as a low-band filter blocking out the signal above 42kHz.
>
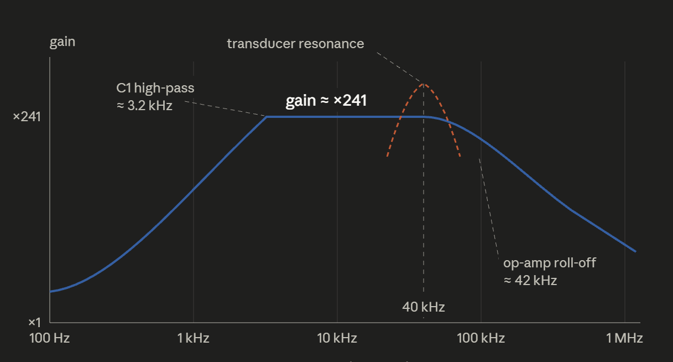
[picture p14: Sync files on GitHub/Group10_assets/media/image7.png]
> 
>
> Since the transducer picks up a signal centered at 40kHz, we will get a signal mostly consisting of a frequency around 40kHz.

**<u>Testing</u>**

### **<u>2. Envelope Detector</u>**

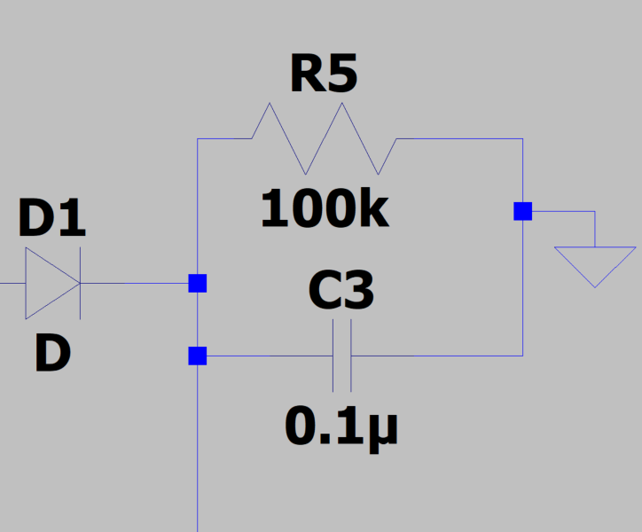
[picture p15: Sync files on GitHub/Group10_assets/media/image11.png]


Problem : Pure signal from the previous stages outputs a high frequency AC signal.

We use the envelope detector which takes in high-frequency modulated signals and outputs its ‘envelope’ which is a smooth curve that outlines the peak of the original waveform.

Explain that a microcontroller cannot process a high frequency signal since it would require a massive amount of processing power for high-frequency sampling.

### **<u>3. Comparator Stage - Schmitt Trigger Hysteresis</u>**

Problem : Amplitude of the signal is not constant, it fluctuates very much depending on the distance from sensor to the rock.

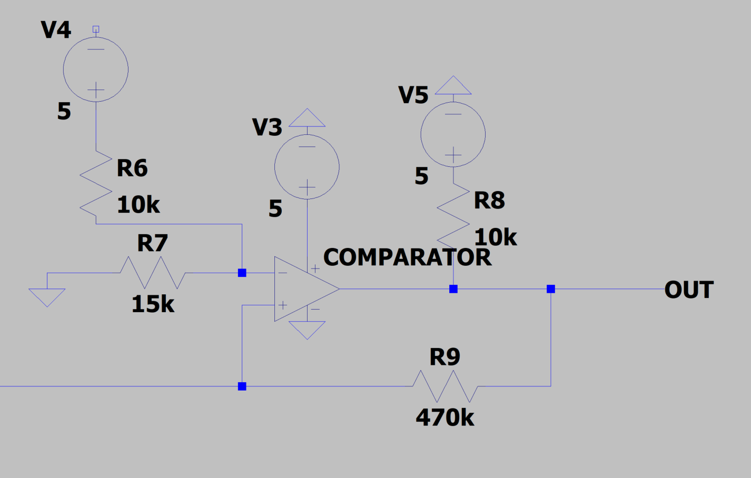
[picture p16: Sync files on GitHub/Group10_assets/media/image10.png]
Circuit diagram of comparator stage.


We convert the smoothed analogue signal from envelope stage into a digital \`High\` or \`Low\` logic signal that can be used to represent the presence of an ultrasonic signal. This is done by setting a reference voltage and when the signal crosses the threshold, the output snaps cleanly to a digital logic signal.

Explain about Schmitt trigger, and show the calculation for the upper threshold and lower threshold.

Also we can verify this using an oscilloscope and a power supply. By viewing how the output of a comparator changes as you change the input voltage.

## **<u>Evaluation of Ultrasonic Subsystem.</u>**

**<u>Verification of the circuit.</u>**

The circuit has been tested for each part of the circuit.

1)  

I can use the oscilloscope’s signal generator to verify that the circuit cuts out the frequencies below and above the set domain of frequency.

\[ Picture of the oscilloscope : Using signal generator in oscilloscope\]

\[ Multiple pictures of the oscilloscope showing the change in the signal\]

2)  Envelope Detector.

\[ Multiple pictures of the oscilloscope showing the change in the signal\]

3)  Comparator - Schmitt trigger

> \[ Picture of the signal in oscilloscope\]

As you can see from the photo above, output is a clean DC logic voltage. With 5V as HIGH and 0V as LOW.

This will be connected to a digital pin of an arduino and be used to detect a presence of signal.

\[ Multiple pictures of the oscilloscope showing the change in the signal\]

**<u>Others</u>**

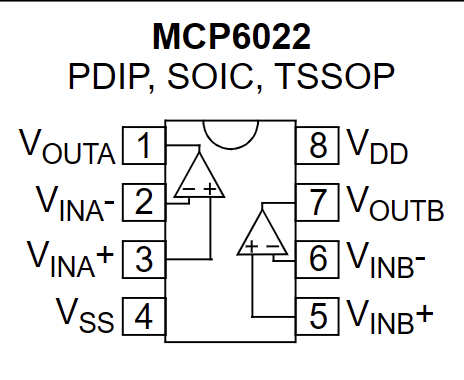
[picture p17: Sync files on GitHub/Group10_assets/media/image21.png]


**Datasheet for MCP6022 : [<u>https://ww1.microchip.com/downloads/aemDocuments/documents/MSLD/ProductDocuments/DataSheets/MCP6021-Data-Sheet-DS20001685.pdf</u>](https://ww1.microchip.com/downloads/aemDocuments/documents/MSLD/ProductDocuments/DataSheets/MCP6021-Data-Sheet-DS20001685.pdf)**

**Datasheet for LM393P :**

[**<u>https://www.ti.com/lit/ds/symlink/lm2903b.pdf?ts=1780888870193</u>**](https://www.ti.com/lit/ds/symlink/lm2903b.pdf?ts=1780888870193)

**This is the circuit diagram of the ultrasonic subsystem.**



**INFRARED DETECTION (CHRIS)**

**<u>BACKGROUND</u>**

The types of a rock is indicated by an infrared signal pulse rate with a Poisson distribution, ultrasonic signal and magnetic fields. For infrared signal, you have already made a light sensor as part of the EEEBug and most <span class="mark">silicon-based photosensors</span> (such as the EEEBug phototransistor) are just as sensitive to infrared as visible light. You will need to measure the infrared pulses rate and this can be done with <span class="mark">analogue or digital methods</span>.

The optical power given by the rock is weaker than the light source you used for the EEEBug so you may need to amplify the output. Ambient light will cause interference and this can be <span class="mark">filtered out by using a sensor that is only sensitive to the wavelength of the rock emission (950nm) and by using electronic filters</span>. Many sources of electric light have a strong frequency component at 100Hz due to the rectification effect of the 50Hz AC source.

The infrared <span class="mark">pulse rate</span> is approximately λ=547 s-1 or λ=312 s-1 depending on the type of a rock. The <span class="mark">pulse width</span> of the infrared signal is just <span class="mark">50μs</span> and the <span class="mark">amplitude</span> that you observe <span class="mark">will be reduced if you filter out the high frequency harmonics</span>. <span class="mark">Low-pass filtering</span> may smooth out the edges of the pulse and <span class="mark">make pulse rate measurement less accurate</span>. There can even be a problem with the sensor itself, since all optical sensors have a capacitance that acts to introduce a low-pass filter. There may be a <span class="mark">trade-off between the speed and the sensitivity of your sensor.</span>

A recommended method for measuring random infrared pulse rates on a lab oscilloscope is described below.

1.  View pulses on the oscilloscope with a 10ms timebase.

2.  Add measurement for 'Count' (positive or negative pulse depending on signal).

3.  Use the 'single' button to capture and count one screen of the signal. The oscilloscope shows 12 divisions at 10ms, so the measurement is the pulses counted in 120ms.

4.  You can confirm that the count measurement matches the number of pulses visible on the screen, but you should use the 'Zoom' view to be able to distinguish closely spaced pulses.

5.  Use the single button to make as many measurements as necessary to get a statistically significant result.

6.  Measuring the infrared pulses rate on the oscilloscope



**<u>EEEBug Phototransistor</u>**

A phototransistor acts like a <span class="mark">light-dependent current source</span>. It requires a <span class="mark">bias voltage to work and a load resistor in series</span> to convert the current into a voltage that can be measured by the ADC. Additionally, a <span class="mark">capacitor can be added to create a low-pass filter that will remove any high-frequency noise</span>.

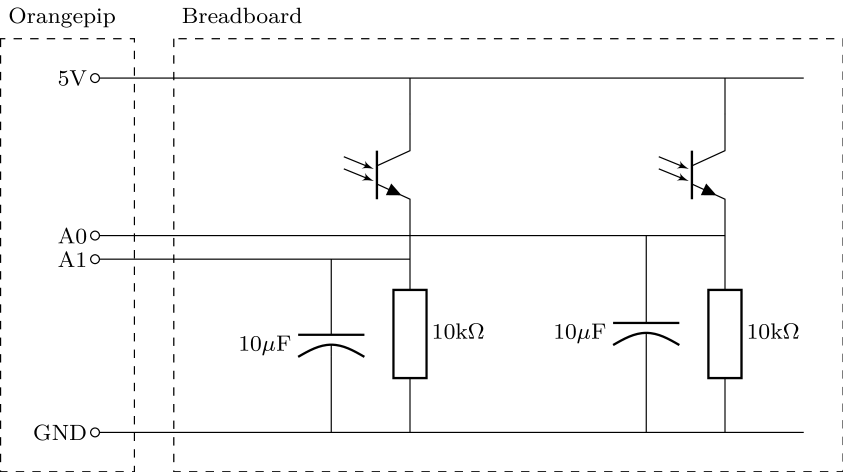
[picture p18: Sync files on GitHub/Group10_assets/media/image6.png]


**<u>Design Log</u>**

**14/05**

Based on the background info + the EEE lab skills section on sensing, I ascertain that the key implement required to achieve infrared detection will involve a phototransistor.

The phototransistor acts as a light dependent current source. Since phototransistors are similarly sensitive to infrared radiation as they are to the visible light spectrum, they can be implemented here to detect IR. I theorise that I can implement a phototransistor that will send bursts of current to the metro board upon receiving IR, which can then be interpreted using proper arduino code to determine the frequency of the IR.

Some things to consider will be implementation of the filtering of ambient light, filtering of noise, while maintaining sensitivity and speed of the sensor.

<table style="width:96%;">
<colgroup>
<col style="width: 96%" />
</colgroup>
<thead>
<tr>
<th>Current train of thought for implementation</th>
</tr>
<tr>
<th><p>Receive signal -&gt; filter for 950nm -&gt; amplify -&gt; filter noise -&gt; interpret -&gt;</p>
<p>return value</p></th>
</tr>
</thead>
<tbody>
</tbody>
</table>

For now, the arduino code is superficial, I need to focus on how to implement the filtering and amplification for detection, before the interpretation stage. I realise there are two possible methods to achieve the detection:

1.  Optical Filter -\> amplify

- I can achieve this by attaching a physical filter to the phototransistor, using it to directly filter out light for wavelength 950nm.

- Then amplify using an opamp of some kind

> Advantages:

- Prevents unwanted light from generating current at all

<!-- -->

- Reduces saturation from ambient light

- Improves signal-to-noise ratio (SNR)

- Keeps the amplifier from amplifying unwanted signals

- Relatively simple implementation

2.  Amplify -\> electronic filter

Advantages

- Small signals become easier to process

- Active filters often require some gain anyway

Disadvantages:

- Noise and interference also get amplified

- Large unwanted signals can overload the amplifier before filtering

3.  Electronic filter -\> amplify

Advantages:

- Prevents out-of-band noise from entering the amplifier

- Reduces risk of overload/saturation

- Better dynamic range

Disadvantages:

- Passive filters may attenuate the desired signal too

- If the signal is already tiny, filter losses can hurt SNR

I note the demo conditions to determine what would be best. There is quite a lot of ambient light and the optical power given by the rock is weaker than the light source used for the sensing experiment (this was an iPhone torchlight). Hence, I determine that the best approach would be to combine method 1 and 2.

Combining method 1 and 2 would filter the IR in two stages. First, using the optical filter, unwanted ambient light will be filtered out from the 950nm wavelength we want to detect. Then, amplification so that the small signal is magnified for proper detection (electronic filtering first could result in loss of signal). Finally, electronic filtering using a band-pass filter to allow the desired frequencies of 312 and 547 to be “selected”.

**BREAK**

I noted that I was wrong in identifying what to measure to identify the rock types. The rocks emit IR using a poisson distribution, which is not equivalent to frequency. The pulse rates of 312 and 547 are not constant across the time they are measured for. [<u>https://www.youtube.com/watch?v=jmqZG6roVqU</u>](https://www.youtube.com/watch?v=jmqZG6roVqU) I watched this video to remind myself of the poisson distribution and relevant calculations. I will revisit this when determining how to interpret the signal data from the phototransistor.

I now determine what parts will be needed to start testing of my proposed detection method. I will need a phototransistor of course, followed by an opamp that can provide the gain and electronic filtering.

When deciding what type of phototransistor to use, I must pay attention to the spectral response, the speed and the viewing angle. [<u>https://www.wevolver.com/article/photo-transistor-comprehensive-guide-for-modern-engineers</u>](https://www.wevolver.com/article/photo-transistor-comprehensive-guide-for-modern-engineers)

<table style="width:96%;">
<colgroup>
<col style="width: 24%" />
<col style="width: 71%" />
</colgroup>
<thead>
<tr>
<th>Spectral Response</th>
<th>should be around 950nm (the wavelength of the IR from the rocks)</th>
</tr>
<tr>
<th>Speed</th>
<th><p>should be greater than the signal bandwidth to prevent pulse smearing which will affect the calculation of lambda.</p>
<p>The pulse width of the IR pulses is related to the signal bandwidth. Pulse width (W) is the duration of a signal (t), while Bandwidth (BW) is the range of frequencies (Hz). For many applications, the bandwidth is the reciprocal of the pulse width: (BW =1/W).</p>
<p>The pulse width is 50microseconds which gives a bandwidth of 20kHz.</p></th>
</tr>
<tr>
<th>Viewing angle</th>
<th>should be narrower to reduce noise that is picked up and enable a more directed detection method (benefit: start counting from earlier time when moving towards rock, improve lambda calculation. Con: must be pointed towards target)</th>
</tr>
</thead>
<tbody>
</tbody>
</table>

What is available in EEEstores:

| SD0127 | PHOTOTRANSISTOR 5mm,HALF ANGLE 50° | £0.35 |
|---|---|---|

When deciding the type of opamp to use, I must pay attention to the gain-bandwidth product and the slew rate and the operating voltage.

<table style="width:96%;">
<colgroup>
<col style="width: 23%" />
<col style="width: 72%" />
</colgroup>
<thead>
<tr>
<th>GBP</th>
<th>Frequency at which gain becomes 1. Must make sure that the GBP of the chosen opamp is not at the detection frequency range otherwise will not be able to amplify the signal much for proper interpretation</th>
</tr>
<tr>
<th>Slew rate</th>
<th><p>The slew rate of an operational amplifier is the maximum rate of change of its output voltage. This will limit the speed of amplification.</p>
<p>The pulsewidth is 50microseconds, which means that for optimised processing speed, the opamp slew rate must be equal to or higher than 50microseconds so it can respond quickly to the rise and falls in IR signal due to the short pulses.</p>
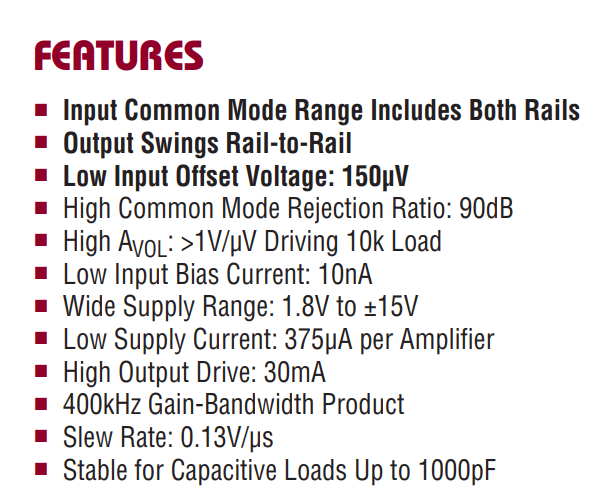
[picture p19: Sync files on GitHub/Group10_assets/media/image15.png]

<p>The LT1366 opamp has a slew rate of 0.13V/us which is very low and unideal for this detection</p></th>
</tr>
<tr>
<th>Operating voltage</th>
<th>The voltage required to drive the opamp. The metro board has built in 5V and 3.3V regulators. The chosen opamp must be able to operate at either of these voltages or a combination of the two.</th>
</tr>
</thead>
<tbody>
</tbody>
</table>

**BREAK**

The last step of my research progress for today is to determine suitable candidates for the phototransistor and opamp parts to be ordered for testing next monday.

First, I determine pulse width, pulse rate and required timing accuracy. Then I choose a detector with sufficient bandwidth, then an amplifier bandwidth somewhat above detector bandwidth. Choose GBP from: required gain × required bandwidth

Using a 940nm peak wavelength phototransistor to detect a 950nm IR source is highly effective and widely considered a standard pairing. Because phototransistors have a broad spectral response, they maintain nearly full sensitivity within a few dozen nanometers of their peak. \[[<u>1</u>](https://uk.farnell.com/kingbright/l-53p3c/phototransistor-5mm-940nm/dp/2290444), [<u>2</u>](https://grobotronics.com/led-5mm-950nm-100mw.html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), [<u>3</u>](https://www.researchgate.net/publication/311624207_High-Performance_Near-Infrared_Phototransistor_Based_on_n-Type_Small-Molecular_Organic_Semiconductor), [<u>4</u>](https://botland.store/blog/phototransistor-what-is-it-and-what-is-it-used-for/)\]

Performance & Compatibility

- High Sensitivity: Most 940nm phototransistors are designed to be "spectrally matched" to emitters ranging from 870nm to 950nm.

- Minimal Efficiency Loss: While you aren't hitting the absolute peak (940nm), the drop in sensitivity at 950nm is typically negligible (often less than 5–10%), as the response curve for silicon-based sensors is relatively flat at these near-infrared wavelengths.

- Broad Bandwidth: A typical 940nm phototransistor can actually detect light across a massive range, often from 400nm to 1100nm. Manufacturers specify 940nm as the peak simply to indicate where it is most efficient. \[[<u>1</u>](https://uk.farnell.com/vishay/vemt3700f-gs08/photo-transistor-npn-940nm-plcc/dp/2504153), [<u>2</u>](https://www.futurlec.com/LED/INFD5940TRANS.shtml), [<u>3</u>](https://electronics.stackexchange.com/questions/478121/will-a-950-nm-ir-emitter-work-with-a-870-nm-phototransistor), [<u>4</u>](https://johnloomis.org/ece445/topics/egginc/pt_char.html), [<u>5</u>](https://uk.farnell.com/kingbright/l-53p3c/phototransistor-5mm-940nm/dp/2290444)\]

Practical Considerations

- Daylight Filters: Many 940nm phototransistors (like the [<u>Vishay VEMT3700F</u>](https://uk.farnell.com/vishay/vemt3700f-gs08/photo-transistor-npn-940nm-plcc/dp/2504153)) come with a "daylight blocking" black lens. This filter is specifically designed to allow IR light between 870nm and 950nm to pass while blocking visible light, making it ideal for your 950nm source.

I decided to end my research here. I will select a phototransistor with built in daylight blocking lens with appropriate remaining parameters and a corresponding opamp tomorrow

**15/05**

Continuing from my previous research, I began searching for an ideal phototransistor on Mouser. I found the following two transistors which could be ideal for detection.

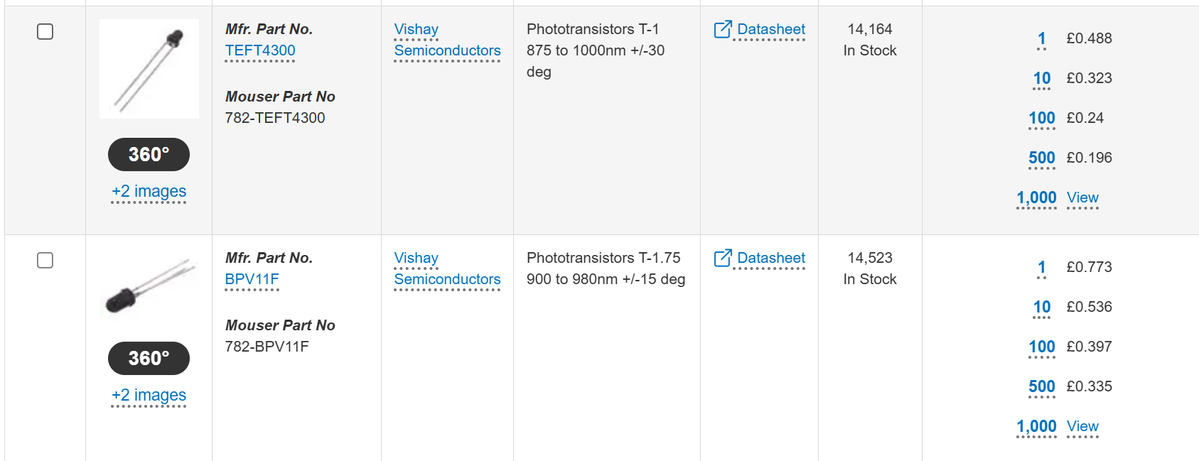
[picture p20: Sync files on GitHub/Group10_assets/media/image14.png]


| TEFT4300 | https://www.vishay.com/docs/81549/teft4300.pdf |
|---|---|
| BPV11F | https://www.vishay.com/docs/81505/bpv11f.pdf |

The TEFT4300 and the BPV11F are two transistors that are suitable for this application. Both have a black lens coating that filters out visible light so I can pinpoint the wavelength of IR to be measured. Both spectral wavelength ranges and rise and fall times are adequate for detecting the 950nm 50-microsecond-width pulses. The key difference is the viewing angle. TEFT4300 is 30 while the BPV11F is 15. The BPV11F smaller viewing angle can further minimise ambient noise and distortion. It might be worth it to purchase both and test both.

As for the opamp, I choose one based on GBP and slew rate. Slew rate should be at least 5V/us to be safe. As for GBP, I have to determine that based on the gain I want to implement for the signal detection. I will go into the lab and test the detection method with the existing phototransistor and LT1366 to see the pulses before determining the desired gain. A key concern is managing the circuit package size.

**BREAK**

I now move onto testing the infrared detection method as proposed in the github. I replicated the phototransistor sensor setup detailed in the sensor lab skills section like so:



I configured the arduino code to run on the metro board and then ran a simulation using my torchlight to confirm that the detector works as per normal. I then used the rock simulator to perform an IR detection test.

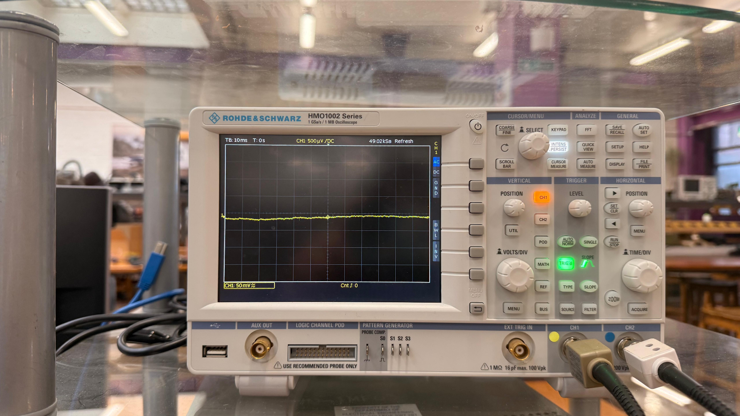
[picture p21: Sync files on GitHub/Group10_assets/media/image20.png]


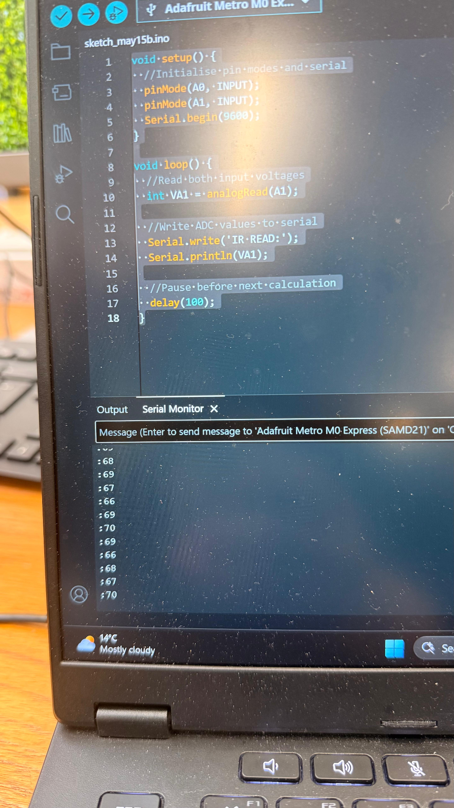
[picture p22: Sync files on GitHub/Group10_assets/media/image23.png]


I couldn’t obtain any noticeable pulses on the oscilloscope or the serial monitor when testing with the rock simulator, even though the phototransistor was sensitive to light. I realised that the capacitor in parallel might be affecting the detection of pulses as capacitors act as filters. I then removed the capacitor and found that the pulses were now being detected as spikes on the oscilloscope and large value jumps on the serial monitor.

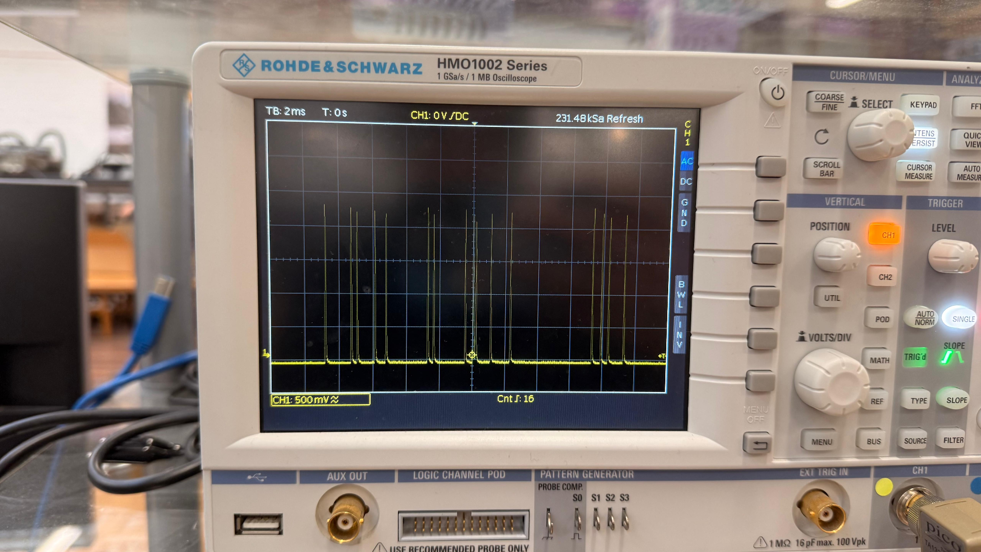
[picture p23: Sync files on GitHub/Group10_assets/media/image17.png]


I note that the signal is detected when the diode points at roughly mid level to the internal PCB of the rock simulator. Upon covering the internal PCB with the rock case, I observed that the pulses had dropped significantly. I could only see very small pulses, as shown below:



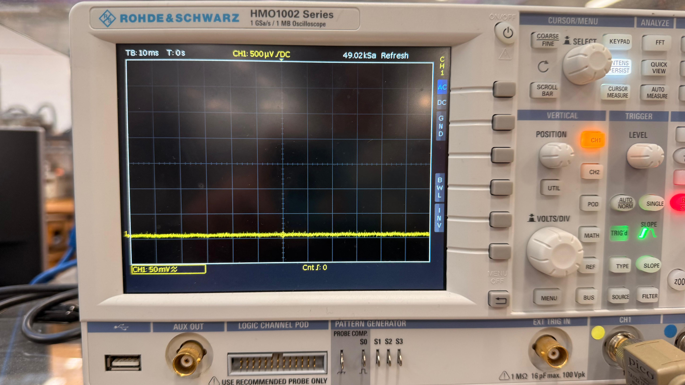
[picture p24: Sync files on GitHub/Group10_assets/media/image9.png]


With this in mind, I believe a gain of 10-20 would be sufficient to amplify the signal back to a readable value.

After researching, the AD8032 is a suitable opamp for amplification use:

[<u>https://www.mouser.co.uk/datasheet/3/1014/1/AD8031_8032.pdf</u>](https://www.mouser.co.uk/datasheet/3/1014/1/AD8031_8032.pdf)

GBP is 80MHz, which when providing a gain of 20 results in a bandwidth of 4MHz, plenty of bandwidth to spare when the cutoff frequency of the detector diode is only around 110kHz. Gives leeway for higher magnitude gain if needed.

Slew rate is 30V/us which far exceeds the pulse width, will be able to respond quickly.

Can operate from 2.7 to 12V, suitable range as access to 3.3V and 5V voltage nodes.

Is also dual channel, can be used for amplification of other detection circuits so as to maximise breadboard space efficiency.

Changed to MCP6022I/P (explain why later)

**22/05**

All parts needed have arrived, proper design testing begins. First reconfigure test setup using new parts. Keep in mind digital pins 6,4,3,2 used for motor control

Bought TEFT and BPV to test and compare. First set up using TEFT

[<u>https://www.youtube.com/watch?v=zNAbcUSptWE</u>](https://www.youtube.com/watch?v=zNAbcUSptWE)

Determine the gain, start with a test of gain = 10, easiest choice of resistors is 10k and 100k -\> gain = 11 (non-inverting) INSERT PIC OF nodal analysis circuit drawing

Detection pre opamp successful using TEFT4300, insert pics, scale for V = 10V. Upon covering w rock, need to increase scale to 50mV to obtain visible pulse, large drop off due to rock interference

Implement opamp

Note, check original signal detection, why amplitude so high? If too high cannot be fed into opamp, would explain why opamp not working

Tab 2

# Albert Ma — Movement & UI Logbook

Personal work log for the Movement / Web UI module of the EEE Lunar Rover (Group 10).\
Maintained here as a draft; the contents are periodically copy-pasted into the team's Google Doc.

## Date: 13 May 2026

### 👥 Team Organization & Task Allocation

- First team meeting at the EE lab (10am, table near the demo area). Held an initial team introduction session.

- Defined and allocated project roles across the team:

  - Mohammed Salem + me: Arduino movement code + user interface

  - Devesh Kemani: Magnetism detection

  - Christopher Koh: Project Manager + Infrared detection

  - Wangmo Koo: Ultrasonic detection + Parts IC

  - Ye Zifan: Age detection

### 🛠️ Hardware & Assembly Progress

- Assembled the basic physical chassis of the EEE Lunar Rover.

- Initial motor diagnostic surfaced two issues:

  - One motor was running noticeably weaker than the other.

  - **Left motor was wired into the right motor's pin on the PCB** (swapped at the PCB level) — flagged for follow-up; later worked around in software (see the 18 May setMotor() HIGH/LOW swap).

- After bench fixes, confirmed the H-bridge driver and differential steering are functional.

### 💻 Software & Project Management

- Set up the team's **central GitHub repository** (Albert14736/EEELunarRover2526-main): created the base branch structure, defined the Sync files on GitHub/ workspace convention (so planning/progress files stay separated from individual code workspaces), wrote the root README, and added Chris, Mohammed, and Zifan as collaborators.

- Standardised the team's docs on **Markdown** so progress, instructions, and embedded screenshots can live alongside the code.

- Migrated existing project planning, schedules, and trackers from Notion into the repo so everything is in one version-controlled place.

- Briefly evaluated **VS Code Live Share** as a real-time collaboration option; team consensus was to stick with GitHub to keep the workflow simple.

### 🎮 Web UI & Movement Control (Major Milestone)

- Developed the complete C++ backend for WiFi remote control, including an automated **500 ms "Watchdog"** safety mechanism that auto-stops the rover if the network connection drops.

- Designed and implemented a responsive **"Hold-to-drive" Web UI** with a live command-history log for debugging. Deployed a temporary UI prototype via GitHub Pages for easy mobile access (this prototype was for backend adaptation/testing only — production UI is now served from the board itself, see 18 May).

- Surveyed the team on **"Tank-style" (rotate-on-the-spot) vs "Car-style" (turn-while-moving) steering**; team picked Tank-style and the C++ backend was implemented accordingly.

- Briefly discussed adding **joystick / analog control**; deferred — the Metro M0 has limited compute headroom (the course brief notes it can't run Python scripts), so we chose to stabilise the simple discrete-direction implementation first.

- Added quality-of-life UI features: per-second connection heartbeat with on-screen "Connected/Disconnected" indicator, 4 diagonal curve buttons (one wheel 200, other wheel 100), a scrollable command history block with an expandable full-screen view, and **WASD / arrow-key keyboard control** for desktop use.

- Wrote field test instructions (WiFi_Testing_Instructions.md) for the team to execute in the lab.

### 📅 Next Steps

- Next team meeting on the afternoon of 15 May to finalize sensor implementation strategies and integrate the frontend UI with the backend C++ motor control.

## Date: 15 May 2026

### 👥 Team Meeting (Hybrid)

- Second team meeting at the EE lab, 1pm. Devesh, Chris, and I attended in person; Mohammed joined remotely via Teams at 2:30pm.

- Agenda: share each member's individual research progress, discuss the overall rover plan, and rectify outstanding issues with the current build.

### 🌐 Networking Architecture Discussion

- Worked through how the rover receives signals over WiFi with Chris:

  - The EEERover network is a closed local-only WiFi — it has no internet access and only routes packets between devices connected to it. So it effectively acts as the intermediate "server" between the controller (phone / laptop) and the rover.

  - This means our existing implementation (HTTP requests from a browser on the same network) works without needing a separate backend server. If we ever wanted to control the rover from a device not on EEERover, we'd need to stand up our own server (e.g. run one on a laptop) as the intermediate.

  - Confirmed the static-IP setup: WiFi.config(IPAddress(192, 168, 0, groupNumber + 1)) with groupNumber = 10, giving the rover the stable address 192.168.0.11.

### 🛒 Procurement Discussion

- Discussed components for each sub-team's sensor implementation. Originally (per the 13 May plan) we had aimed to finalize the bill of materials today, but the team agreed more research was still needed on a few items, so the final BOM decision was **pushed to a follow-up online meeting** (later held on 18 May).

- Wangmo shared the supplier guidance (item name + item number, watch out for pack-of-10 quantities) so people could continue their parts research in the meantime; she would batch-order through the EEED website once the BOM is locked in.

- No new parts needed for the Movement / UI module, so nothing to submit from my side.

### 📡 Cross-team Status (for context)

- Zifan reported the antenna coil for age detection failed initial testing — the standard plastic-coated copper wire only measured ~5 µH on the LCR meter, too low. He proposed switching to proper enamelled magnet wire and asked whether parts can be sourced outside the EEEStore.

### 📋 Admin

- Filled in the participation form (deadline 18 May 7pm).

### 📅 Next Steps

- Reconvene online to finalize the BOM once everyone's parts research is in (later held on 18 May).

- In the meantime, continue working individually — fleshing out research, refining code, and updating personal progress logs for the eventual report.

## Date: 18 May 2026

### 🎮 Web UI & Movement Control

- Implemented the **autonomous Web UI** build — UI no longer depends on the GitHub Pages prototype; the full HTML/CSS/JS is now served directly from the Metro M0 via **PROGMEM** (keeps the page in flash to save SRAM).

- Restored the **advanced UI** features after the autonomous refactor: WASD / arrow-key control, command history log, connection-status indicator, and the sensor dashboard placeholder.

- Added a **cache-buster** (?t=\<timestamp\>) to every HTTP request. Without it, the browser was caching movement commands, so repeated taps on the same direction button were silently dropped.

### 🛠️ Hardware & Motor Control

- Shipped a **stable 5-way movement build** (Forward / Backward / Left / Right / Stop). Earlier builds were running out of SRAM and the WiFi stack would crash intermittently — PROGMEM fixed this.

- **Extended the build to full 8-way movement** later in the day — added the four diagonal directions (Forward-Left, Forward-Right, Backward-Left, Backward-Right) on top of the 5-way base. Inner wheel runs at 40% of the outer wheel speed for smoother diagonal turns. The Web UI's 3×3 directional grid now maps 1:1 to these 8 + Stop.

- Tuned **PWM scaling** so the motors respond proportionally to commands rather than running flat-out only.

- **Fixed the reversed forward/backward bug** by swapping the HIGH / LOW levels in setMotor(). Root cause: the motor wires are inverted relative to the H-bridge's expected polarity, so the software logic had to be inverted to match the actual wiring.

### 👥 Team Meeting (Online)

- Held the **follow-up online meeting** carried over from 15 May. Main agenda was finalizing the **bill of materials** — after the additional days of research, the team locked in which components need to be ordered (sensors, etc.). I'm not responsible for procurement myself, but attended to stay in the loop on what hardware the sensor sub-teams will be working with.

### 💻 Software & Project Management

- Synced **Devesh's magnetism detection** progress from his Google Doc into the repo under Tasks/Magnetism Detection/ so his hardware/code notes live alongside the rest of the project.

### 📅 Next Steps

- *(TODO: fill in any further team decisions if any)*

## Date: 22 May 2026

### 💻 Software & Tooling

- Built an automated **Google Docs sync pipeline** (sync-gdocs.sh at the repo root). One command: rclone pulls the team's master .docx from Drive's "Shared with me", pandoc converts it to GitHub-flavored Markdown, and embedded images are extracted into Sync files on GitHub/Group10_assets/media/. No more manual re-export.

- Added a project-root .gitignore to keep macOS .DS_Store files out of the repo.

- **Pushed two outstanding local commits** to GitHub that had been sitting unpushed since 18 May — including the backward-bug fix and the advanced Web UI restoration. The remote had been running an older buggy version until today.

### 🗂️ Project Management

- Investigated setting up a parallel **Notion sync** for the team's "Engineering Project Tracker". Blocked by Notion permissions — my account only has read access, which doesn't allow adding the Integration required for API access. To unblock, will follow up with Christopher (PM) to either grant Full access or temporarily publish-to-web for an audit.

### 📅 Next Steps

- *(TODO: fill in)*

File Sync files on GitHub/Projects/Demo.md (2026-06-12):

# Final Demo

**Date of Assessment:** 16 June 2026
**Weighting:** 40%

## Demo Format
1. **Lab Bench Assessment**: The examiner will ask to see different functional aspects and assess our theoretical understanding of the implementation.
2. **Arena Demonstration**: A head-to-head competition on the simulated lunar surface to classify all the rocks in the quickest time.

## Pre-flight Checklist (Crucial)
- [ ] **Weight Check**: Total weight MUST be strictly under 750g (to avoid failing in the Weight Sensitive Zone).
- [ ] **Battery**: Fully charged.
- [ ] **WiFi Stability**: Web remote control connects instantly.
- [ ] **Sensors Calibrated**: 
  - Radio (89kHz) decoding works.
  - IR pulses (312/547 Hz) distinguishable.
  - Ultrasound (40kHz) detects presence.
  - Magnetometer correctly identifies Up/Down.

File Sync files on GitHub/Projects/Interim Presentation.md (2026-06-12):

# Interim Presentation 

**Date of Assessment:** 28 May 2026
**Weighting:** 20%

## Objective
Show our progress mid-way through the project. We need to prepare a presentation showing our high-level design, research, technical progress so far, and a plan for the remaining work.

## Presentation Outline (Draft)
1. **System Overview**: High-level block diagram of the EEELunarRover.
2. **Hardware Progress**: 
   - Motor testing results (Done on 13/05)
   - Sensor research (Infrared, Ultrasonic, Magnetic, Radio)
3. **Software Progress**: 
   - Arduino motor control logic (Completed)
   - WiFi & Web interface framework
4. **Remaining Plan**: 
   - PCB/Breadboard integration
   - Final chassis laser cutting

## Tasks for Presentation
- [ ] Create presentation slides
- [ ] Draft the script for each member
- [ ] Rehearse timing

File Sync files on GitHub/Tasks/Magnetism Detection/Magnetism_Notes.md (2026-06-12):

# Magnetism Detection - Research & Design

## Hardware Configuration
- **Sensor**: SS49E Hall Effect Sensor
- **Amplification**: MCP6002 Op-amp (Non-inverting amplifier) to be built on a breadboard if the signal is too weak.
- **Wiring**:
    - Pin 1 (VCC): 3.3V on Metro board.
    - Pin 2 (GND): GND.
    - Pin 3 (Output): Analog Pin (e.g., A0).

## Logic & Calibration
- **Neutral Point**: ~1.65V (Analog value ~512).
- **Polarity**:
    - **North (UP)**: Voltage rises toward 3.3V (Value -> 1023).
    - **South (DOWN)**: Voltage drops toward 0V (Value -> 0).
- **Calibration**: The setup should account for magnetism from motors and zero it out during `setup()`.
- **Filtering**: Use a **Rolling Average** (e.g., average of the last 4 snapshots using an array) to prevent noise from small fluctuations.
- **Interference**: Need to account for potential magnetic fields from other nearby rocks.

## Positioning
- **Orientation**: Point the face (side with writing) down and point forward (closest to the rock).
- **Location**: Position it furthest away from the motors to minimize interference.
- **Mounting**: Plan to 3D print a mount that connects to the pins.

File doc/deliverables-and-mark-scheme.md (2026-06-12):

# Mark Scheme
### Interim Presentation
|**Weighting of presentation in module mark** | **20/100** |
| --- | --- |

| Area of Assessment							| Weighting | High Mark | Medium Mark | Low Mark |
| --- |  --- | --- | --- | --- |
| Requirements Capture			| 20/100 | • Original requirements expanded into project specific requirements <br> • Quantitative specifications given where appropriate <br> • Requirements for subsystems | • Project requirements are expanded and customised |• Project aims are given, but there is some ambiguity |
| System Design | 30/100 | • Strong reasoning for system design decisions <br> • All blocks and interfaces defined <br>| • Core elements of the system are defined <br> • The system design is mostly plausible | • Some important blocks or interfaces in the system are undefined <br> • Unreasonable assumptions about how parts of the design will work|
| System Implementation | 30/100 | • Evidence that all system interfaces are implemented, using emulation or placeholder data where necessary <br> • Some implementation of functionality in each subsytem <br> • Some infrastructure is in place for evaluation | • Some progress on subsystem implementation <br> • Some progress on system interfaces allowing interaction of some subsystems | • Some subsystem implementation but little attempt at system integration ||
| Project Management					| 20/100 | • All group member roles are defined<br> • Risks and contingencies identified<br> • Significant contribution of each group member<br> • Project management framework adopted | • Clear division of work between group members | • Roles of group members are unclear ||

### Report
|**Weighting of presentation in module mark** | **40/100** |
| --- | --- |
|**Word limit** | **10000** |

| Area of Assessment							| Weighting | High Mark | Medium Mark | Low Mark |
| --- |  --- | --- | --- | --- |
|Design Process| 20/100 | • Logical progression of design from top-level requirements to detailed implementation and evaluation <br> • Discussion of all important design decisions with quantitative and qualitative evidence <br> • Interesting discussion of project planning and organisation | • Requirements in place for most of the functionality of the system <br> • Discussion of design decisions, but some unclear reasoning and/or unimportant details <br>  • Full breakdown of task allocation to group members | • Some elaboration of requirements beyond original points in project brief <br> • Some discussion of design decisions, but important aspects given trivial or no reasoning ||
| Implementation | 60/100 |• Design is a technically complex system of interacting components <br> • Advanced techniques and skills are applied, requiring research beyond module content <br> | • Design is a mostly-functional system, maybe some elements are not integrated <br> • Design makes good use of EEE/EIE module content | • Elements of the project are designed, but the project is not functional as a complete system <br> • Some design elements are technically plausible ||
| Evaluation | 20/100| • Evidence that tests all requirements <br> • Evaluation of top-level system and individual subsystems <br> • Appropriate tests and metrics devised <br> • Informative visual presentation of data |• Evaluation of most requirements <br> • Use of quantitative and qualitative data | • Some elements of the design are evaluated, but some important aspects are omitted <br> • Low-quality evidence of design outcome |

### Professional Practice and Individual Reflection Form 
|**Weighting of reflection in module mark:** | **0/100** |  **Must pass component. You must pass each component** |
| --- | --- | --- |

| Area of Assessment							| Pass |
| --- | --- |
| EDI | Adopt an inclusive approach to engineering practice and recognise the responsibilities, benefits and importance of supporting equality, diversity and inclusion |
| Teamwork |Function effectively as an individual, and as a member or leader of a team. Evaluate effectiveness of own and team performance|
| Lifelong Learning | Plan and record self-learning and development as the foundation for lifelong learning/CPD|

### Interview and Demonstration
|**Weighting of presentation in module mark** | **40/100** |
| --- | --- |

| Area of Assessment							| Weighting | High Mark | Medium Mark | Low Mark |
| --- |  --- | --- | --- | --- |
| Functionality | 30/100 | • The system works very well, with few flaws <br> • The user interaction is intuitive <br> • Some elements are technically astounding |• Integrated demonstration that shows most elements of the project working together <br> • Demo gives an impression of the overall user interaction | • Demo of independent elements of the project without complete integration <br> • Demo shows project outcome but leaves viewer confused about which elements work properly <br> • Requests to recompile or reconfigure the system during demo to show different elements | 
| Technical Insight | 40/100 | • Detailed reasoning is given for questions about design and implementation <br> • Question responses show complete understanding of technical challenges and solutions <br> • Plausible suggestions for addressing flaws |• Answers to most questions show understanding of technical details <br> • Justification for most design and implementation decisions <br> • Honest discussion of limitations | • Elements of the project are demonstrated but there is a dubious explanation about why they work or don't work <br> • Third-party libraries are demonstrated without discussion about their limitations, or how they should be integrated into the system |
|Group Working | 30/100 | • Clear role for each group member in the implementation <br> • Each group member makes a strong contribution to question and answer <br> • Interaction of project subsystems shows close cooperation between group members | • All group members contribute to the discussion <br> • Evidence that group members have collaborated on system integration <br> | • Some group members don't contribute to the discussion, making their contribution unclear. <br> • Elements of the project are mostly independent from each other, showing a lower amount of cooperation |

> [!NOTE]
> Information from the demo may be used to adjust the report mark. For example, this could arise where
claims in the report do not match evidence from the demo, or the report did not give a true sense of
the complexity of a project element

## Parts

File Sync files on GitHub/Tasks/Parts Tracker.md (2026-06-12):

# Parts Tracker & Order List

**Total Budget:** £60.00
**Parts IC (Approver):** Wangmo Koo

*Note: All orders must be approved by the Parts IC to avoid duplication. Use the Online Order Form in EEE Stores Website.*

## Components to Order (Draft)

| Item | Use Case | Cost (£) | Min Quantity | Status |
| :--- | :--- | :--- | :--- | :--- |
| **SS49E hall sensor** | Magnetic Detection | < 1 | | Proposing |
| | | | | |
| | | | | |
| | | | | |
| | | | | |

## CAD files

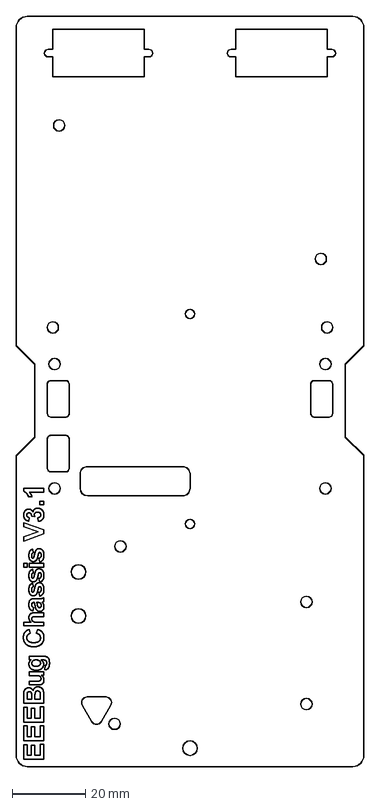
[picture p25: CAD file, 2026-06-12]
mech/chassis.dxf
95.0 x 205.0 mm

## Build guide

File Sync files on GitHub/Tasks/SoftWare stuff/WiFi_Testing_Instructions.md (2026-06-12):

# WiFi Remote Control - Field Test Instructions

**Objective:** Test the full integration of the C++ backend and the Web UI frontend, ensuring the rover can be driven via a mobile phone over a local network.

**Files in this folder:**
- `wifi_rover_control.ino`: The final C++ source code to be uploaded to the rover.
- `remote_ui_test.html`: A local HTML file to preview the UI on any device without connecting to the rover.
- `WiFi_Testing_Instructions.md`: This instruction file.

---

## Phase 0: Hardware Wiring (CRITICAL!)
Because the WiFi Shield actively uses pins **5, 7, 10, 11, 12, and 13**, we MUST NOT plug any motor wires into them, or the WiFi will crash instantly.

Please connect the motor driver (H-Bridge) to the Metro M0 board exactly as follows:
- **Left Motor:**
  - `DIR` (Blue wire)  -> **Pin 2**
  - `EN`  (Orange wire)-> **Pin 3**
- **Right Motor:**
  - `DIR` (Blue wire)  -> **Pin 4**
  - `EN`  (Orange wire)-> **Pin 6**

⚠️ **COMMON GROUND WARNING:** Ensure that the GND pin on the motor driver board is physically connected to the GND pin on the Metro M0 board. If they don't share the same ground, the motors will not spin!

## Phase 1: Uploading the Code (The Brain)
1. Connect the Adafruit Metro M0 board (with the WiFi shield attached) to the lab computer via USB.
2. Open the `wifi_rover_control.ino` file in VS Code (PlatformIO) or Arduino IDE.
3. Verify the WiFi credentials in the code:
   - `ssid`: `"EEERover"`
   - `pass`: `"exhibition"`
   - `groupNumber`: `10` (Since you are Group 10, this sets your static IP to `192.168.0.11`).
4. **Upload/Flash** the code to the Metro M0 board.
5. Open the **Serial Monitor** (Baud rate: 9600). You should see:
   - `Connecting to SSID: EEERover`
   - `Connected!`
   - `IP Address: 192.168.0.11` (Take note of this IP).

## Phase 2: Network Connection & Power Up
1. Turn on the 6V battery pack on the rover to provide power to the H-Bridge motor drivers.
2. Unplug the USB cable if you want to test fully wireless (the Metro board will now draw power from the battery).
3. Take out your mobile phone and connect to the lab's WiFi network: **`EEERover`** (Password: **`exhibition`**).

## Phase 3: Opening the Web UI
1. Open a web browser (Chrome/Safari) on your phone.
2. Type the IP address exactly as shown in the Serial Monitor (e.g., `http://192.168.0.11`) into the address bar and press Enter.
3. The "Lunar Rover PRO" control panel with the directional arrows (▲ ◀ ▶ ▼) should load on your screen.

### Alternative: Previewing the UI Remotely
You can preview the UI anytime, anywhere, using the public link below. This is great for checking the look and feel, but it won't actually control the rover.

**Public URL:** `https://Albert14736.github.io/EEELunarRover2526-main/Sync%20files%20on%20GitHub/Tasks/SoftWare%20stuff/remote_ui_test.html`

## Phase 4: Execution & Observation Checklist

- [ ] **Forward Test:** Press and *hold* the **▲ (FWD)** button. 
  - *Expected:* Both wheels spin forward.
  - *Troubleshooting:* If the rover moves backward, the motor wires are inverted. We can easily fix this by changing `SPEED` to `-SPEED` in the `moveForward()` C++ function.
- [ ] **Stop Logic:** Release the **▲** button. 
  - *Expected:* The rover stops immediately (Hold-to-drive logic works).
- [ ] **Spin Left:** Press and hold **◀ (LFT)**. 
  - *Expected:* Left wheel spins backward, right wheel spins forward. The rover spins on the spot.
- [ ] **Spin Right:** Press and hold **▶ (RGT)**. 
  - *Expected:* Left wheel spins forward, right wheel spins backward.

## Phase 5: The "Watchdog" Safety Test (Crucial)
We have implemented a 500ms timeout watchdog to prevent the rover from crashing if it loses the WiFi connection.
1. Press and hold the **▲ (FWD)** button so the rover keeps moving.
2. While still holding the button on the screen, use your other hand to **turn off your phone's WiFi** (or close the browser).
3. *Expected:* The rover MUST stop automatically within 0.5 seconds. It should NOT keep driving indefinitely.

---
*If all tests pass, the Movement & UI module is 100% complete!*

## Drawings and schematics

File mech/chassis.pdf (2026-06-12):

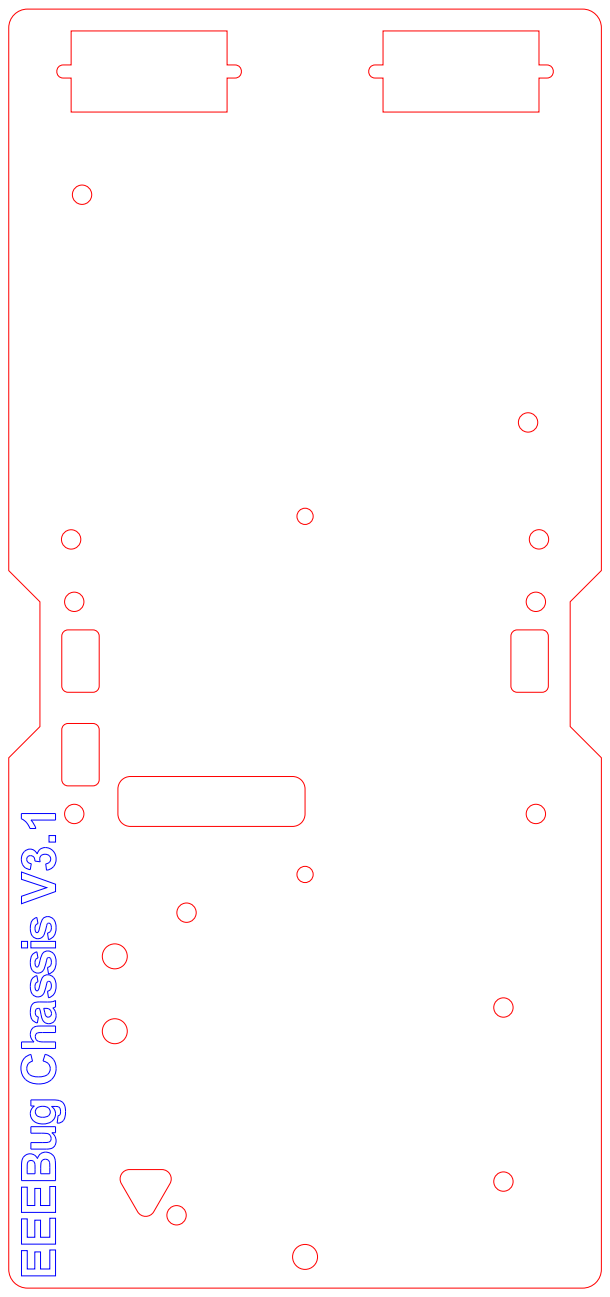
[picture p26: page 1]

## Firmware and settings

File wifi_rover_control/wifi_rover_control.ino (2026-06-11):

#define USE_WIFI_NINA         false
#define USE_WIFI101           true
#include <WiFiWebServer.h>

// ==========================================
// 1. Motor pin definitions
// ==========================================
const int EN_LEFT   = 3;  // left motor PWM (D3 — D2 has no PWM on the M0, so swapped with DIR)
const int DIR_LEFT  = 2;  // left motor direction (D2, digital only)
const int EN_RIGHT  = 4;  // right motor PWM
const int DIR_RIGHT = 6;  // right motor direction

int SPEED = 200;  // motor speed, set at runtime via /speed

// ==========================================
// Infrared sensor (rock type): interrupt pulse counter -> pulse rate
// ==========================================
const int IR_PIN = 9;                  // D9
volatile unsigned long pulseCnt = 0;   // volatile: written inside the ISR
unsigned long lastIRTime = 0;
float IRpulseRate = 0;
void countPulse() { pulseCnt++; }      // ISR: +1 per pulse

// ==========================================
// Magnetism sensor (rock type): analogue Hall on A4 -> up/down/none
// ==========================================
const int MAG_PIN = A4;                // A4

// ==========================================
// Radio / age: Serial1 (D0 RX) at 600 baud, ASCII digits per reading
// ==========================================
const int AGE_BUF = 40;
char ageBuf[AGE_BUF];                   // digit run currently being accumulated
int  ageLen = 0;
// Mode filter: keep recent 3-digit readings in a 2s window, serve the most frequent
// one. The '#'-delimited stream is noisy (44/445/4443), so corrupt variants lose the vote.
const unsigned long AGE_WIN = 2000;     // voting window (ms)
const int AGE_N = 64;                   // ring buffer capacity
int           ageVals[AGE_N];           // recent 3-digit reading values (0..999)
unsigned long ageTimes[AGE_N] = {0};    // their arrival times (0 = empty slot)
int           ageHead = 0;

// ==========================================
// Ultrasound sensor (rock type): digital read on D8 -> 40kHz present/absent
// ==========================================
const int US_PIN = 12;                   // D8 (moved back after the hardware fix)

// ==========================================
// 2. WiFi Configuration
// ==========================================
const char ssid[] = "Albert iPhone";   // iPhone Personal Hotspot
const char pass[] = "12345678";
const int groupNumber = 10;            // (only used for the lab EEERover static IP)

WiFiWebServer server(80);

// ==========================================
// 3. Web UI Frontend
// ==========================================
const char webpage[] PROGMEM = R"rawliteral(
<!DOCTYPE html>
<html>
<head>
  <meta charset="UTF-8">
  <meta name="viewport" content="width=device-width, initial-scale=1, maximum-scale=1, user-scalable=no">
  <style>
    body { font-family: sans-serif; text-align: center; background: #222; color: #fff; margin-top: 50px; user-select: none; -webkit-user-select: none; }
    .grid { display: grid; grid-template-columns: repeat(3, 90px); grid-gap: 15px; justify-content: center; margin-top: 30px; }
    .btn { width: 90px; height: 90px; font-size: 20px; font-weight: bold; border-radius: 15px; border: none; background: #4CAF50; color: white; touch-action: manipulation; }
    .btn:active { background: #45a049; }
    .btn.active-state { background: #45a049; }
    .stop { background: #f44336; }
    #status-box { margin-top: 40px; padding: 15px; background: #111; border-radius: 10px; width: 80%; max-width: 300px; margin-left: auto; margin-right: auto; font-family: monospace; color: #0f0; word-wrap: break-word;}
    #history-box { margin-top: 15px; padding: 15px; background: #1a1a1a; border-radius: 10px; width: 80%; max-width: 300px; margin-left: auto; margin-right: auto; font-family: monospace; color: #aaa; height: 120px; overflow-y: auto; text-align: left; box-sizing: border-box; position: relative; }
    .expand-btn { position: absolute; top: 10px; right: 10px; background: #333; color: #fff; border: 1px solid #555; padding: 3px 8px; border-radius: 5px; cursor: pointer; font-size: 10px; }
    .dashboard { margin-top: 20px; padding: 15px; background: #111; border-radius: 10px; width: 80%; max-width: 300px; margin-left: auto; margin-right: auto; text-align: left; border: 1px solid #444; }
    .dash-item { margin: 10px 0; font-size: 13px; display: flex; justify-content: space-between; border-bottom: 1px dashed #333; padding-bottom: 5px; }
    .dash-label { color: #ccc; }
    .dash-val { color: #f44336; font-family: monospace; }
    .speed-control { margin-top: 25px; width: 80%; max-width: 300px; margin-left: auto; margin-right: auto; }
    .speed-control label { display: block; font-size: 14px; margin-bottom: 8px; color: #ccc; }
    #speed-slider { width: 100%; height: 30px; }
    #speed-num { width: 55px; background: #111; color: #4CAF50; border: 1px solid #555; border-radius: 5px; font-family: monospace; font-weight: bold; font-size: 14px; text-align: center; padding: 3px; }
  </style>
</head>
<body oncontextmenu="return false;">
  <h2>Lunar Rover PRO V5</h2>
  <div id="connection-indicator" style="font-size:18px; font-weight:bold; color:#f44336; margin-bottom:15px;">❌ Disconnected</div>
  <div id="rock-id" style="font-size:16px; font-weight:bold; color:#FFD54F; margin-bottom:15px;">—</div>

  <div class="grid">
    <button id="btn-fl" class="btn" onmousedown="startMove('/forward_left')" ontouchstart="startMove('/forward_left')">&#8598;</button>
    <button id="btn-fwd" class="btn" onmousedown="startMove('/forward')" ontouchstart="startMove('/forward')">&#9650;</button>
    <button id="btn-fr" class="btn" onmousedown="startMove('/forward_right')" ontouchstart="startMove('/forward_right')">&#8599;</button>
    <button id="btn-lft" class="btn" onmousedown="startMove('/left')" ontouchstart="startMove('/left')">&#9664;</button>
    <button id="btn-stp" class="btn stop" onmousedown="stopMove()" ontouchstart="stopMove()">STOP</button>
    <button id="btn-rgt" class="btn" onmousedown="startMove('/right')" ontouchstart="startMove('/right')">&#9654;</button>
    <button id="btn-bl" class="btn" onmousedown="startMove('/backward_left')" ontouchstart="startMove('/backward_left')">&#8601;</button>
    <button id="btn-bwd" class="btn" onmousedown="startMove('/backward')" ontouchstart="startMove('/backward')">&#9660;</button>
    <button id="btn-br" class="btn" onmousedown="startMove('/backward_right')" ontouchstart="startMove('/backward_right')">&#8600;</button>
  </div>

  <div class="speed-control">
    <label>Speed: <input type="number" id="speed-num" min="60" max="255" step="1" value="200"> / 255</label>
    <input type="range" id="speed-slider" min="60" max="255" value="200">
  </div>

  <div class="dashboard">
    <div style="color: #fff; text-align: center; margin-bottom: 10px; font-weight: bold;">Sensor Dashboard</div>
    <div class="dash-item"><span class="dash-label">📡 Radio</span> <span class="dash-val" id="age-val">--</span></div>
    <div class="dash-item"><span class="dash-label">🧲 Magnetic</span> <span class="dash-val" id="mag-val">--</span></div>
    <div class="dash-item"><span class="dash-label">🔥 Infrared</span> <span class="dash-val" id="ir-val">--</span></div>
    <div class="dash-item"><span class="dash-label">🦇 Ultrasound</span> <span class="dash-val" id="us-val">Pending</span></div>
  </div>

  <div id="status-box">Status: Ready...</div>
  <div id="history-box">
    <div style="color: #fff; border-bottom: 1px solid #444; padding-bottom: 5px; margin-bottom: 5px; text-align: center; font-size: 12px;">Command History</div>
    <div id="history-content" style="font-size: 12px;"></div>
  </div>

  <script>
    var timer;
    var currentAction = "";
    var historyContent = document.getElementById('history-content');

    function sendCmd(cmd) {
      var xhttp = new XMLHttpRequest();
      xhttp.onreadystatechange = function() {
        if (this.readyState == 4 && this.status == 200) {
          document.getElementById('status-box').innerHTML = "Status: " + this.responseText;
        }
      };
      var url = cmd + "?t=" + new Date().getTime();
      xhttp.open('GET', url, true);
      xhttp.send();
    }

    var minRtt = 99999;
    setInterval(function() {
      var t0 = new Date().getTime();
      var pxhttp = new XMLHttpRequest(); pxhttp.open('GET', '/ping?t=' + t0, true); pxhttp.timeout = 500;
      pxhttp.onload = function() {
        var rtt = new Date().getTime() - t0;
        if (rtt < minRtt) minRtt = rtt;
        document.getElementById('connection-indicator').innerHTML = '✅ Connected · ' + rtt + ' ms (min ' + minRtt + ')';
        document.getElementById('connection-indicator').style.color = '#4CAF50';
      };
      pxhttp.onerror = function() {
        document.getElementById('connection-indicator').innerHTML = '❌ Disconnected';
        document.getElementById('connection-indicator').style.color = '#f44336';
      };
      pxhttp.send();
    }, 1000);

    // Poll all sensors in one combined request (cuts the per-second 5-request burst).
    // SENSOR_POLL_MS is the only knob: lower = fresher dashboard but more socket
    // contention with drive commands; higher = snappier control. 250ms is the balance.
    var SENSOR_POLL_MS = 250;
    setInterval(function() {
      var sx = new XMLHttpRequest(); sx.open('GET', '/sensors?t=' + new Date().getTime(), true); sx.timeout = 800;
      sx.onload = function() {
        if (sx.status != 200) return;
        var p = sx.responseText.split('|');
        if (p.length < 5) return;
        document.getElementById('ir-val').innerHTML = p[0];
        document.getElementById('mag-val').innerHTML = p[1];
        document.getElementById('us-val').innerHTML = p[2];
        document.getElementById('age-val').innerHTML = p[3];
        document.getElementById('rock-id').innerHTML = p[4];
      };
      sx.send();
    }, SENSOR_POLL_MS);

    function startMove(cmd) {
      if (currentAction !== cmd) {
        var log = document.createElement('div');
        log.innerHTML = "> " + cmd;
        historyContent.insertBefore(log, historyContent.firstChild);
        currentAction = cmd;
      }
      document.getElementById('status-box').innerHTML = "Sending: " + cmd;
      sendCmd(cmd);
      clearInterval(timer);
      timer = setInterval(function() { sendCmd(cmd); }, 200);
    }

    function stopMove() {
      clearInterval(timer);
      currentAction = "";
      sendCmd('/stop');
    }

    // WASD & Arrow Keys Support
    var keyState = { w:0, a:0, s:0, d:0, arrowup:0, arrowleft:0, arrowdown:0, arrowright:0 };
    function processKeys() {
      var fwd = keyState['w'] || keyState['arrowup'];
      var bwd = keyState['s'] || keyState['arrowdown'];
      var lft = keyState['a'] || keyState['arrowleft'];
      var rgt = keyState['d'] || keyState['arrowright'];

      var cmd = "/stop";
      if (fwd && lft) cmd = "/forward_left";
      else if (fwd && rgt) cmd = "/forward_right";
      else if (bwd && lft) cmd = "/backward_left";
      else if (bwd && rgt) cmd = "/backward_right";
      else if (fwd) cmd = "/forward";
      else if (bwd) cmd = "/backward";
      else if (lft) cmd = "/left";
      else if (rgt) cmd = "/right";

      if (cmd === "/stop") stopMove(); else startMove(cmd);
    }

    document.addEventListener('keydown', function(e) {
      if (e.target && e.target.tagName === 'INPUT') return; // don't drive while typing in a field
      var key = e.key.toLowerCase();
      if (keyState[key] !== undefined && !keyState[key]) {
        keyState[key] = 1; processKeys();
      }
    });
    document.addEventListener('keyup', function(e) {
      var key = e.key.toLowerCase();
      if (keyState[key] !== undefined) {
        keyState[key] = 0; processKeys();
      }
    });

    document.addEventListener('mouseup', stopMove);
    document.addEventListener('touchend', stopMove);

    // Speed control: slider + number box, clamped 60-255
    var speedSlider = document.getElementById('speed-slider');
    var speedNum = document.getElementById('speed-num');
    function clampSpeed(v) {
      v = parseInt(v, 10);
      if (isNaN(v)) v = parseInt(speedSlider.value, 10); // fall back to current value
      return Math.max(60, Math.min(255, v));             // clamp to 60-255
    }
    function applySpeed(v) {
      speedSlider.value = v;
      speedNum.value = v;
      document.getElementById('status-box').innerHTML = "Speed set: " + v;
      var sx = new XMLHttpRequest();
      sx.open('GET', '/speed?v=' + v + '&t=' + new Date().getTime(), true);
      sx.send();
    }
    speedSlider.addEventListener('input', function() { speedNum.value = this.value; });            // live-sync number box
    speedSlider.addEventListener('change', function() { applySpeed(clampSpeed(this.value)); this.blur(); });
    speedNum.addEventListener('change', function() { applySpeed(clampSpeed(this.value)); });        // clamp + send on enter/blur
  </script>
</body>
</html>
)rawliteral";

// ==========================================
// 4. Core Motor Functions
// ==========================================
unsigned long lastCmdTime = 0;
const unsigned long WATCHDOG_TIMEOUT = 500;

void replyAPI(const String& msg) {
  server.sendHeader(F("Access-Control-Allow-Origin"), F("*"));
  server.send(200, F("text/plain"), msg);
}

// Fine trim for residual straight-line drift (left wheel now has real PWM on D3).
// Start at 1.0; lower it if it veers right, raise toward 1.0 if it veers left.
const float LEFT_TRIM = 1.0;

void setMotor(int dirPin, int enPin, int speed) {
  if (enPin == EN_LEFT) speed = (int)(speed * LEFT_TRIM);
  if (speed == 0) {
    analogWrite(enPin, 0);
  } else if (speed > 0) {
    digitalWrite(dirPin, HIGH); // HIGH = forward
    analogWrite(enPin, speed);
  } else {
    digitalWrite(dirPin, LOW);  // LOW = reverse
    analogWrite(enPin, -speed);
  }
}

void stopBoth() { setMotor(DIR_LEFT, EN_LEFT, 0); setMotor(DIR_RIGHT, EN_RIGHT, 0); }
void moveForward() {
  Serial.println("Cmd: Forward");
  setMotor(DIR_LEFT, EN_LEFT, SPEED); setMotor(DIR_RIGHT, EN_RIGHT, SPEED);
  lastCmdTime = millis(); replyAPI(F("Fwd"));
}
void moveBackward() {
  Serial.println("Cmd: Backward");
  setMotor(DIR_LEFT, EN_LEFT, -SPEED); setMotor(DIR_RIGHT, EN_RIGHT, -SPEED);
  lastCmdTime = millis(); replyAPI(F("Rev"));
}
void turnLeft() {
  Serial.println("Cmd: Left");
  setMotor(DIR_LEFT, EN_LEFT, -SPEED); setMotor(DIR_RIGHT, EN_RIGHT, SPEED);
  lastCmdTime = millis(); replyAPI(F("Left"));
}
void turnRight() {
  Serial.println("Cmd: Right");
  setMotor(DIR_LEFT, EN_LEFT, SPEED); setMotor(DIR_RIGHT, EN_RIGHT, -SPEED);
  lastCmdTime = millis(); replyAPI(F("Right"));
}
void curveForwardLeft() {
  int inner = (SPEED * 4) / 10;
  Serial.print("Cmd: Curve Fwd Left (L:"); Serial.print(inner); Serial.println(", R:200)");
  setMotor(DIR_LEFT, EN_LEFT, inner); setMotor(DIR_RIGHT, EN_RIGHT, SPEED);
  lastCmdTime = millis(); replyAPI("C-FL (" + String(inner) + "/200)");
}
void curveForwardRight() {
  int inner = (SPEED * 4) / 10;
  Serial.print("Cmd: Curve Fwd Right (L:200, R:"); Serial.print(inner); Serial.println(")");
  setMotor(DIR_LEFT, EN_LEFT, SPEED); setMotor(DIR_RIGHT, EN_RIGHT, inner);
  lastCmdTime = millis(); replyAPI("C-FR (200/" + String(inner) + ")");
}
void curveBackwardLeft() {
  int inner = (SPEED * 4) / 10;
  Serial.print("Cmd: Curve Bwd Left (L:"); Serial.print(-inner); Serial.println(", R:-200)");
  setMotor(DIR_LEFT, EN_LEFT, -inner); setMotor(DIR_RIGHT, EN_RIGHT, -SPEED);
  lastCmdTime = millis(); replyAPI("C-BL (" + String(-inner) + "/-200)");
}
void curveBackwardRight() {
  int inner = (SPEED * 4) / 10;
  Serial.print("Cmd: Curve Bwd Right (L:-200, R:"); Serial.print(-inner); Serial.println(")");
  setMotor(DIR_LEFT, EN_LEFT, -SPEED); setMotor(DIR_RIGHT, EN_RIGHT, -inner);
  lastCmdTime = millis(); replyAPI("C-BR (-200/" + String(-inner) + ")");
}
void stopRover() {
  Serial.println("Cmd: Stop");
  stopBoth(); replyAPI(F("Stop"));
}

void handleRoot() {
  server.setContentLength(CONTENT_LENGTH_UNKNOWN);
  server.send(200, F("text/html"), "");
  int totalLength = sizeof(webpage) - 1;
  int bytesSent = 0;
  const int CHUNK_SIZE = 512;
  char chunkBuffer[CHUNK_SIZE + 1];
  while (bytesSent < totalLength) {
    int currentChunkSize = (totalLength - bytesSent > CHUNK_SIZE) ? CHUNK_SIZE : totalLength - bytesSent;
    memcpy_P(chunkBuffer, webpage + bytesSent, currentChunkSize);
    chunkBuffer[currentChunkSize] = '\0';
    server.sendContent(chunkBuffer);
    bytesSent += currentChunkSize;
    delay(20);
  }
  server.sendContent("");
}

void handlePing() { server.send(200, F("text/plain"), F("pong")); }

void handleSpeed() {
  if (server.hasArg("v")) {
    SPEED = constrain(server.arg("v").toInt(), 60, 255); // clamp 60-255 (too low stalls the motors)
  }
  replyAPI(String(SPEED));
}

// IR tiers by pulse rate: <240 = No IR, 240-400 = 312/s, >400 = 547/s
String irStatus() {
  if (IRpulseRate > 400)       return "547";
  else if (IRpulseRate >= 240) return "312";
  else                         return "No IR";
}
void handleIR() { replyAPI(irStatus() + " - " + String((int)IRpulseRate) + "/s"); }

// Magnetism thresholds (single source of truth, shared with rockType)
bool magIsNorth(int v) { return v > 620; }
bool magIsSouth(int v) { return v < 600; }

// Magnetism by ADC value: >620 = Up (N), <600 = Down (S), else None
String magStatus() {
  int v = analogRead(MAG_PIN);
  String dir;
  if (magIsNorth(v))      dir = "UP (North)";
  else if (magIsSouth(v)) dir = "DOWN (South)";
  else                    dir = "None";
  return dir + " - " + String(v);
}
void handleMag() { replyAPI(magStatus()); }

// Most frequent 3-digit reading within the last AGE_WIN ms ("no signal" if none).
String ageBest() {
  unsigned long now = millis();
  int bestVal = -1, bestCount = 0;
  for (int i = 0; i < AGE_N; i++) {
    if (ageTimes[i] == 0 || now - ageTimes[i] > AGE_WIN) continue;
    int c = 0;
    for (int j = 0; j < AGE_N; j++)
      if (ageTimes[j] != 0 && now - ageTimes[j] <= AGE_WIN && ageVals[j] == ageVals[i]) c++;
    if (c > bestCount) { bestCount = c; bestVal = ageVals[i]; }
  }
  if (bestVal < 0) return "no signal";
  char b[4] = { (char)('0' + (bestVal / 100) % 10),
                (char)('0' + (bestVal / 10) % 10),
                (char)('0' + bestVal % 10), 0 };
  return String(b);
}
// Insert the decimal point for display: 3-digit age "444" -> "4.44" (voting/judgment unchanged).
String ageDot() {
  String a = ageBest();
  if (a == "no signal") return a;
  return a.substring(0, 1) + "." + a.substring(1);
}
void handleAge() { replyAPI(ageDot()); }   // dotted age, e.g. "4.44"

// Ultrasound: HIGH = 40kHz detected, LOW = none
String usStatus() { return digitalRead(US_PIN) == HIGH ? "Detected" : "None"; }
void handleUS() { replyAPI(usStatus()); }

// Rock type from IR + ultrasound + magnetism (spec table).
// Any 2 of the 3 signals uniquely identify a rock, so we score each rock by how
// many of its 3 signature conditions match and accept the one scoring >=2. One
// neutral reading (e.g. magnet in the dead zone) still classifies on the other
// two; a flipped reading that ties two rocks stays "Unknown" (no guessing).
struct RockSig { const char* name; bool ir547; bool usYes; bool magUp; };
String rockType() {
  bool ir547 = IRpulseRate > 400;
  bool ir312 = IRpulseRate >= 240 && IRpulseRate <= 400;
  bool usYes = digitalRead(US_PIN) == HIGH;
  int  mv    = analogRead(MAG_PIN);
  bool magUp = magIsNorth(mv);
  bool magDn = magIsSouth(mv);

  static const RockSig sigs[4] = {
    {"Basaltoid", true,  true,  false},   // 547 / 40kHz / Down
    {"Gravion",   false, false, false},   // 312 /  --   / Down
    {"Regolix",   false, true,  true },   // 312 / 40kHz / Up
    {"Lunarite",  true,  false, true },   // 547 /  --   / Up
  };

  int bestScore = 0, bestIdx = -1;
  bool tie = false;
  for (int i = 0; i < 4; i++) {
    int s = 0;
    if (sigs[i].ir547 ? ir547 : ir312)  s++;
    if (sigs[i].usYes ? usYes : !usYes) s++;
    if (sigs[i].magUp ? magUp : magDn)  s++;
    if (s > bestScore)       { bestScore = s; bestIdx = i; tie = false; }
    else if (s == bestScore) { tie = true; }
  }
  if (bestIdx >= 0 && bestScore >= 2 && !tie) return sigs[bestIdx].name;
  return "Unknown";
}
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
void loop() {
  server.handleClient();
  if (millis() - lastCmdTime > WATCHDOG_TIMEOUT) { stopBoth(); }

  // IR: every ~500ms, pulse rate = pulse count / elapsed time
  unsigned long irElapsed = millis() - lastIRTime;
  if (irElapsed >= 500) {
    noInterrupts();
    unsigned long cnt = pulseCnt;
    pulseCnt = 0;
    interrupts();
    lastIRTime = millis();
    IRpulseRate = (float)cnt * 1000.0 / (float)irElapsed;
    if (Serial) { Serial.print("IR rate: "); Serial.print((int)IRpulseRate); Serial.print("/s -> "); Serial.println(irStatus()); }
  }

  // Radio/age: collect digits; any non-digit ('#', '?', line noise) ends a reading.
  // Stream is '#'-delimited with no newlines. 3-digit readings vote in the 2s buffer;
  // ageBest() returns the most frequent (noise variants lose).
  int ageBudget = 32;
  while (Serial1.available() && ageBudget-- > 0) {
    char c = Serial1.read();
    if (c >= '0' && c <= '9') {
      if (ageLen < AGE_BUF - 1) ageBuf[ageLen++] = c;
    } else {                                       // any non-digit ends a reading
      if (ageLen == 3) {                           // only 3-digit readings vote
        ageVals[ageHead] = (ageBuf[0]-'0')*100 + (ageBuf[1]-'0')*10 + (ageBuf[2]-'0');
        ageTimes[ageHead] = millis();
        ageHead = (ageHead + 1) % AGE_N;
      }
      ageLen = 0;                                  // start next reading
    }
  }
}

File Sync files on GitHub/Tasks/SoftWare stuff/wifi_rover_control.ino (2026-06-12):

#define USE_WIFI_NINA         false
#define USE_WIFI101           true
#include <WiFiWebServer.h>

// ==========================================
// 1. Hardware Pin Definitions
// ==========================================
const int DIR_LEFT  = 2;  // Changed from 12 to 2 to avoid WiFi conflict
const int EN_LEFT   = 3;  // PWM pin for left motor
const int DIR_RIGHT = 9;  // Right motor DIR
const int EN_RIGHT  = 8;  // Right motor PWM

const int SPEED = 200; // Testing speed (0-255), high enough to overcome stiction

// ==========================================
// 2. WiFi Configuration
// ==========================================
const char ssid[] = "EEERover";
const char pass[] = "exhibition";
const int groupNumber = 0; // Set your group number to fix IP at 192.168.0.(groupNumber+1)

WiFiWebServer server(80);

// ==========================================
// 3. Web UI Frontend 
// ==========================================
const char webpage[] = R"rawliteral(
<!DOCTYPE html>
<html>
<head>
  <meta charset="UTF-8">
  <meta name="viewport" content="width=device-width, initial-scale=1, maximum-scale=1, user-scalable=no">
  <style>
    body { font-family: sans-serif; text-align: center; background: #222; color: #fff; margin-top: 50px; user-select: none; -webkit-user-select: none; }
    .grid { display: grid; grid-template-columns: repeat(3, 90px); grid-gap: 15px; justify-content: center; margin-top: 30px; }
    .btn { width: 90px; height: 90px; font-size: 28px; font-weight: bold; border-radius: 15px; border: none; background: #4CAF50; color: white; touch-action: manipulation; }
    .btn:active { background: #45a049; }
    .btn.active-state { background: #45a049; }
    .stop { background: #f44336; }
    .empty { background: transparent; }
    #status-box { margin-top: 40px; padding: 15px; background: #111; border-radius: 10px; width: 80%; max-width: 300px; margin-left: auto; margin-right: auto; font-family: monospace; color: #0f0; word-wrap: break-word;}
    #history-box { margin-top: 15px; padding: 15px; background: #1a1a1a; border-radius: 10px; width: 80%; max-width: 300px; margin-left: auto; margin-right: auto; font-family: monospace; color: #aaa; height: 120px; overflow-y: auto; text-align: left; box-sizing: border-box; position: relative; transition: all 0.3s ease; }
    #history-box.expanded { position: fixed; top: 5%; left: 5%; right: 5%; bottom: 5%; width: 90%; height: 90%; max-width: none; z-index: 1000; font-size: 16px; box-shadow: 0 0 20px rgba(0,0,0,0.8); }
    .expand-btn { position: absolute; top: 10px; right: 10px; background: #333; color: #fff; border: 1px solid #555; padding: 3px 8px; border-radius: 5px; cursor: pointer; font-size: 12px; }
    /* Sensor Dashboard */
    .dashboard { margin-top: 20px; padding: 15px; background: #111; border-radius: 10px; width: 80%; max-width: 300px; margin-left: auto; margin-right: auto; text-align: left; border: 1px solid #444; }
    .dash-item { margin: 10px 0; font-size: 15px; display: flex; justify-content: space-between; border-bottom: 1px dashed #333; padding-bottom: 5px; }
    .dash-label { color: #ccc; }
    .dash-val { color: #f44336; font-family: monospace; font-size: 12px; }
  </style>
</head>
<body>
  <h2>Lunar Rover PRO</h2>
  
  <div id="connection-indicator" style="font-size:18px; font-weight:bold; color:#f44336; margin-bottom:15px;">❌ Disconnected</div>

  <div class="grid">
    <button id="btn-fl" class="btn" onmousedown="startMove('/forward_left')" onmouseup="stopMove()" ontouchstart="startMove('/forward_left')" ontouchend="stopMove()">&#8598;</button>
    <button id="btn-fwd" class="btn" onmousedown="startMove('/forward')" onmouseup="stopMove()" ontouchstart="startMove('/forward')" ontouchend="stopMove()">&#9650;</button>
    <button id="btn-fr" class="btn" onmousedown="startMove('/forward_right')" onmouseup="stopMove()" ontouchstart="startMove('/forward_right')" ontouchend="stopMove()">&#8599;</button>
    <button id="btn-lft" class="btn" onmousedown="startMove('/left')" onmouseup="stopMove()" ontouchstart="startMove('/left')" ontouchend="stopMove()">&#9664;</button>
    <button id="btn-stp" class="btn stop" onmousedown="stopMove()" ontouchstart="stopMove()">STOP</button>
    <button id="btn-rgt" class="btn" onmousedown="startMove('/right')" onmouseup="stopMove()" ontouchstart="startMove('/right')" ontouchend="stopMove()">&#9654;</button>
    <button id="btn-bl" class="btn" onmousedown="startMove('/backward_left')" onmouseup="stopMove()" ontouchstart="startMove('/backward_left')" ontouchend="stopMove()">&#8601;</button>
    <button id="btn-bwd" class="btn" onmousedown="startMove('/backward')" onmouseup="stopMove()" ontouchstart="startMove('/backward')" ontouchend="stopMove()">&#9660;</button>
    <button id="btn-br" class="btn" onmousedown="startMove('/backward_right')" onmouseup="stopMove()" ontouchstart="startMove('/backward_right')" ontouchend="stopMove()">&#8600;</button>
  </div>

  <!-- Sensor Dashboard -->
  <div class="dashboard">
    <div style="color: #fff; text-align: center; margin-bottom: 10px; font-weight: bold;">Sensor Dashboard</div>
    <div class="dash-item"><span class="dash-label">📡 Radio (Age)</span> <span class="dash-val">Wait for Zifan...</span></div>
    <div class="dash-item"><span class="dash-label">🔥 Infrared</span> <span class="dash-val">Wait for Chris...</span></div>
    <div class="dash-item"><span class="dash-label">🦇 Ultrasound</span> <span class="dash-val">Wait for Wangmo...</span></div>
    <div class="dash-item"><span class="dash-label">🧲 Magnetic</span> <span class="dash-val">Wait for Devesh...</span></div>
  </div>

  <div id="status-box">Status: Ready to connect...</div>
  <div id="history-box">
    <button class="expand-btn" onclick="toggleHistory()">Expand</button>
    <div style="color: #fff; border-bottom: 1px solid #444; padding-bottom: 5px; margin-bottom: 5px; text-align: center;">Command History</div>
    <div id="history-content"></div>
  </div>

  <script>
    var timer;
    var heartbeatCount = 0;
    var currentActionName = "";
    var statusBox = document.getElementById('status-box');
    var historyContent = document.getElementById('history-content');

    function getActionName(cmd) {
      if(cmd === '/forward') return 'Forward';
      if(cmd === '/backward') return 'Backward';
      if(cmd === '/left') return 'Left';
      if(cmd === '/right') return 'Right';
      if(cmd === '/forward_left') return 'Forward Left';
      if(cmd === '/forward_right') return 'Forward Right';
      if(cmd === '/backward_left') return 'Backward Left';
      if(cmd === '/backward_right') return 'Backward Right';
      return 'Stop';
    }

    function sendCmd(cmd) {
      if (cmd !== '/stop') heartbeatCount++;
      statusBox.innerHTML = "Transmitting: <strong style='color:#fff; font-size:18px;'>" + cmd + "</strong><br>Packets Sent: " + heartbeatCount;
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
